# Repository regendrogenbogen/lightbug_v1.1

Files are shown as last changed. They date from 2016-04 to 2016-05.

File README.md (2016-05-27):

# lightbug v1.1

Source files for a small light following robot based on the Arduino Leonardo design. 
Hardware design was done in Altium Designer and I am not sure how and under which license I am
allowed to share the sorce files, therefor I am only sharing the Gerbers, schematic and
the BOM. 
According to the Arduino website derivates of the design must be shared under the
Creative Commons Attribution Share-Alike license, I hope that is applicable for the non-source
files I am publishing. Also, I am not really sure if this really counts as a derivate because I
just took the default operating circuit for the ATMega32U4 and added my peripherals.
The software is of course completely open, according to the GPL license.

Have fun with the files!

The PCB can be ordered at OSH-Park: https://oshpark.com/shared_projects/ZxSDuxPU

I have a blog post to this robot: https://regendrogenbogen.wordpress.com/2016/04/29/lightbug-v1-1/

PS: If I did licence anything wrong and I am violating other licenses, please tell me,
I am still learning!

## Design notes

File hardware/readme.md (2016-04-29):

# Hardware design files for the robot

I added the schematic as an PDF and the gerber files

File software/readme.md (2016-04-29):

# Software for the robot

If you build your own robot, you need to set the fuses correctly. I did this with Atmel Studio.
The Production file for the fuses is "Fuses_Lightbug_v1.1.elf". 
If you can't use Atmel Studio, the fuses need to be the following values:
* Extended: 0xFE
* High: 0xD8
* Low: 0xDE
 
After setting the Fuses and installing the Arduino Leonardo Bootloader (Leonardo-prod-firmware-2012-12-10.hex)
you can program the board like any regular Arduino Leonardo.

There are 2 versions:
* one basic which just has the light following ability (software_lightbug_v1_0)
* one with added serial communication with simple commands to control the robot over bluetooth (software_lightbug_v1_1)

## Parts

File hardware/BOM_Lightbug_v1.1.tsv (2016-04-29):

Positions/quantity | Item | Description | order number
 | Farnell
D1 | STPS3L40S | Schottky diode | 2353680
LED1, LED2 | LED 3mm | green | 1142502
3 | LR6/AA Alkaline | Batteries, 120 pcs. | 2470180
R1, R2 | 1k | Resistor, wired | 9341102
R4, R5 | 330R | Resistor, wired | 9341730
4 | 2k4 | Resistor, SMD, for servo hacking | 9332880
LDR1, LDR2 | LDR | Light sensor | 3168335
R6, R7 | 22R | Resistor, SMD | 9332847
IC1 | ATMEGA32U4 | 8 bit, AVR | 1748525
USB1 | Micro USB socket | Type B | 2293753
C4 | 1uF | Ceramic condensator SMD | 1759422
Y1 | Keramikresonator 16MHz | Ceramic resonator 16 MHz | 2470359
C1, C2 | 100nF | Ceramic condensator SMD | 1759167
C3 | 100nF | Ceramic condensator wired | 2112751
2 | washers 2,7mm | Wheel monting | 2253190
R3, R10 | 10k | Resistor, SMD | 2447553
JP2 | Jumper | Power on jumper | 5217908
S1 | OS102011MS2QN1 | 100mA sliding switch, power selector | 1201430
 | Hobbyking
2 | HK15346 | Servo motors, need to be hacked | HK15346
1 | wheels | Pack of 5 | OR006-00809
 | Pololu
1 | ball caster | 3/8 inch Plastic Ball | 950
 | Distrelec
1 | Battery case | 3 x AA | 973233
1 | pin headers | 5,8mm, 2,6mm | 126387

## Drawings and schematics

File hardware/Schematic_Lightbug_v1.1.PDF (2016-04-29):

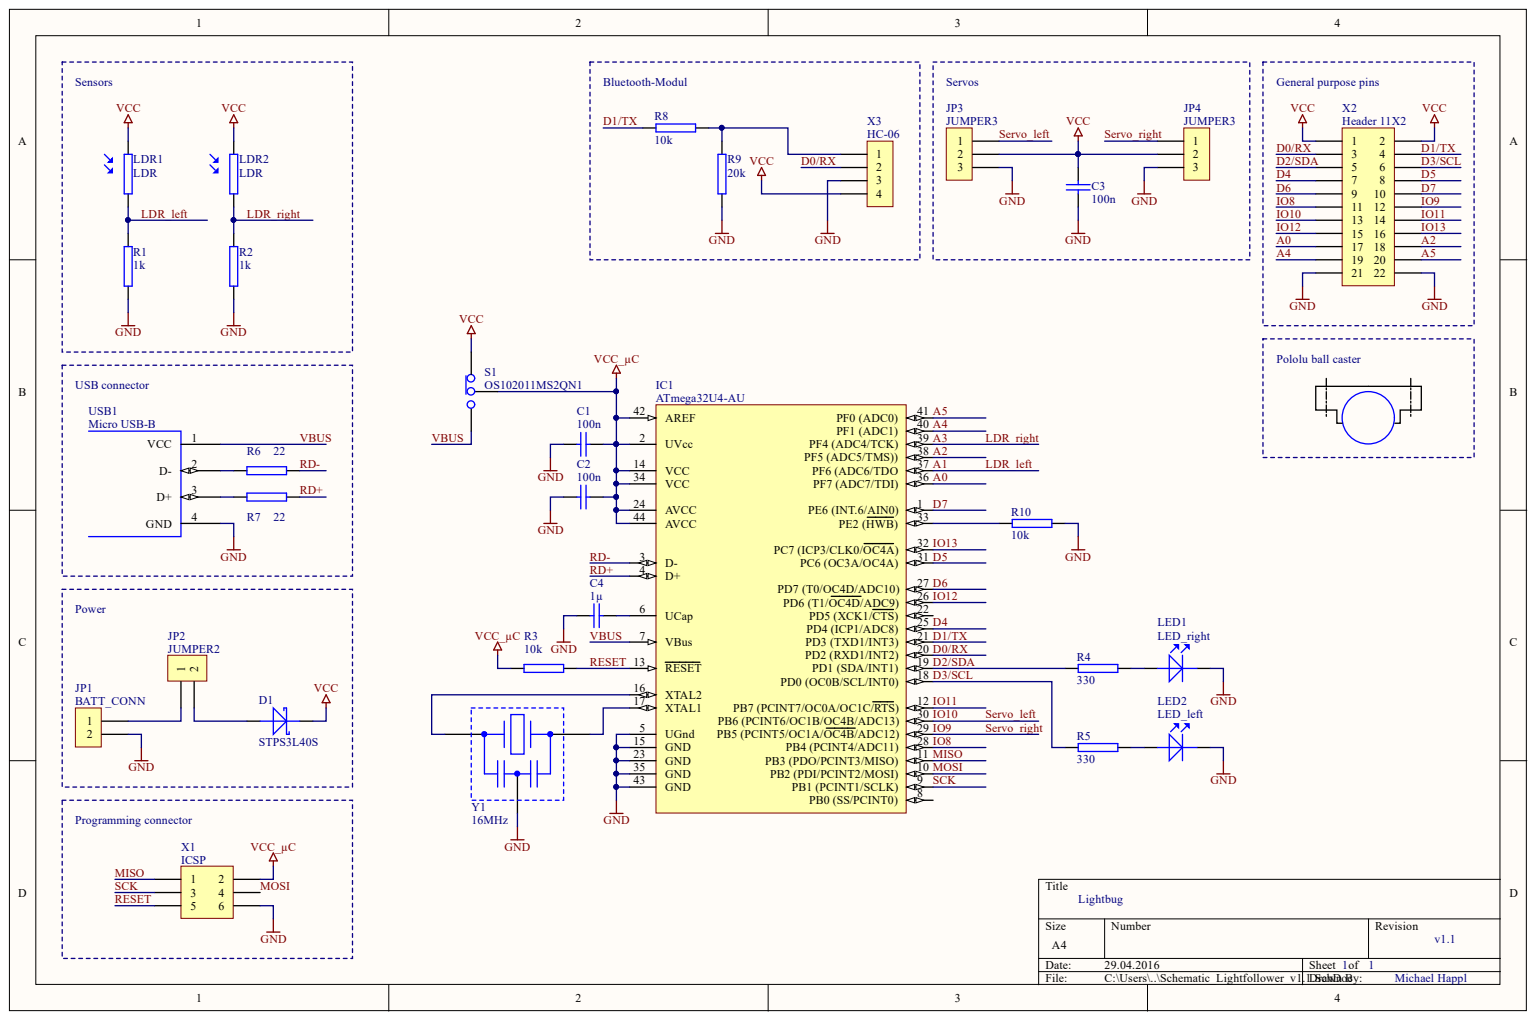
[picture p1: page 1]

XTAL1 17

GND 15 | IO8

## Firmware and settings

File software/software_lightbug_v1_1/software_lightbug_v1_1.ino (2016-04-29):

// Lightbug v 1.1
// by Michael Happl
// based on Lightfollower V1.0 by Johann Leinweber
// Adds a serial communication with simple commands to make it possible
// to control the robot over bluetooth.

#include <Servo.h> 

#define led_left 2           //digital pin for the left LED
#define led_right 3          //digital pin for the right LED
#define led_mode 5           //digital pin for the mode LED
#define servopin_left 10     //digital pin for the left servo
#define servopin_right 9     //didital pin for the right servo
#define servo_high 150       //value for the left servo
#define servo_low 30         //value for the right servo

Servo myservo_left;          //create servo object to control a servo
Servo myservo_right;         //create servo object to control a servo

int left_LDR = A1;           //analog pin used to connect the left LDR
int right_LDR = A3;          //analog pin used to connect the right LDR
int trh_time = 6000;         //time for measuring thresholdvalue in ms
//int time = 0;                //temporary time for measuring time
int val_left = 0;            //variable to read the value from left LDR
int val_right = 0;           //variable to read the value from left LDR
int mean_left = 0;           //meanvalue left LDR
int mean_right = 0;          //meanvalue right LDR
int trh_left = 0;            //threshold for left LDR
int trh_right = 0;           //threshold for right LDR
int loop_time = 10;          //execute loop only every 10ms
unsigned long time = 0;      //variable for measuring time

// State flag
boolean auto_mode = true;

//====================== Serial stuff for the bluetooth module ======================
// constants
#define Baudrate 9600                //baudrate for communicating with the HC-06 Bluetooth module

// variables
boolean debug = 1;                   //Debug mode for testing the commands
boolean command_ok = false;          //indicates finished command receive

char command_string[3];              //the received characters, max. 3
char sensor_left_string[] = "LLX#";  //placeholder for the left sensor value
char sensor_right_string[] = "LRX#"; //placeholder for the rigth sensor value
int char_index = 0;                  //index of the received character


//====================== Setup ======================
void setup()                              //setup, will be executed only once at the start
{   
  pinMode(led_left,OUTPUT);                   //left LED pin as output
  pinMode(led_right,OUTPUT);                  //right LED pin as output
  pinMode(led_mode,OUTPUT);                   //mode LED pin as output
  digitalWrite(led_left, HIGH);               //switch LED left on
  digitalWrite(led_right, HIGH);              //switch LED right on
  digitalWrite(led_mode,LOW);                 //remote controlled mode is off
  delay(5000);                                //wait after power on
  threshold_detect();                         //call routine for thresholddetect
  init_serial();
}                                         //end of setup


//====================== main loop ======================
void loop()                               //main loop
{ 
  receive_characters();                       //receive commands from the bluetooth module
  mode_check();                               //check the command for the current mode
  if ((auto_mode) && (millis() > time))       //run the automatic mode only at a fixed intervall
  {
    time = millis() + loop_time;              //save the current time plus the loop time
    val_left = analogRead(left_LDR);          //left LDR read
    val_right = analogRead(right_LDR);        //right LDR read

    if (val_right > trh_right+40)             //if right LDR is above threshold_right
    {
      servo_left_on(servo_high);              //turn left servo on
    }
    else
    {
      servo_left_off();                       //turn left servo off
    }

    if (val_left > trh_left+40)               //if left LDR is above threshold_left
    {
      servo_right_on(servo_low);              //turn right servo on
    }
    else
    {
      servo_right_off();                      //turn right servo off
    }
    
    sensor_left_string[2] = (char)(val_left / 4);
    send_serial(sensor_left_string);          //send the current left sensor value to the app
    sensor_right_string[2] = (char)(val_right / 4);
    send_serial(sensor_right_string);         //send the current right sensor value to the app
  }                                           //end of automatic mode
  else                                        //begin of remote controlled mode
  { 
    if (command_ok)                           //only if the current command is correct
    {
      if (command_string == "MLF")            //forward left motor
        servo_left_on(servo_high);
      if (command_string == "MLR")            //reverse left motor
        servo_left_on(servo_low);
      if (command_string == "MLO")            //stop left motor
        servo_left_off();
      if (command_string == "MRF")            //forward right motor
        servo_right_on(servo_high);
      if (command_string == "MRR")            //reverse right motor
        servo_right_on(servo_low);
      if (command_string == "MRO")            //stop right motor
        servo_right_off();
    }
  }
}                                         //end of main loop

//====================== servo routines ======================

void servo_left_on (int servo_value)      //routine for turning the left servo on
{
      myservo_left.attach(servopin_left);     //attaches the left servo on pin "left" to the servo object
      myservo_left.write(servo_value);        //left servo turn left
      digitalWrite(led_left, HIGH);           //left LED on
      if (servo_value < 90)
      {
        send_serial("MLR#");                  //send motor left direction to app
      }
      else
      {
        send_serial("MLF#");                  //send motor left direction to app
      }
}                                         //end of servo left on


void servo_left_off ()                    //routine for turning the left servo off
{
      myservo_left.detach();                  //deactivate left servo
      digitalWrite(led_left, LOW);            //left LED off
      send_serial("MLO#");                    //send motor left off to app
}                                         //end of servo left off


void servo_right_on (int servo_value)     //routine for turning the right servo on
{
      myservo_right.attach(servopin_right);   //attaches the right servo on pin "right" to the servo object
      myservo_right.write(servo_value);       //right servo turn right
      digitalWrite(led_right, HIGH);          //right LED on
      if (servo_value < 90)
      {
        send_serial("MRF#");                  //send motor right direction to app
      }
      else
      {
        send_serial("MRR#");                  //send motor right direction to app
      }
}                                         //end of servo right on


void servo_right_off ()                   //routine for turning the right servo off
{
      myservo_right.detach();                 //deactivate right Servo
      digitalWrite(led_right, LOW);           //right LED off
      send_serial("MRO#");                    //send motor right off to app
}                                         //end of servo right off


void threshold_detect ()                  //routine for looking for the average brightness
{
  servo_left_on(servo_high);                 //left servo turn left

  time = millis();
  do
  {
    mean_left = 0;                            //reset variables
    mean_right = 0;                           //reset variables
    for (int i = 0; i<5; i++)                 //5 runs do get average offsetvalues from LDRs
    {
      mean_left += analogRead(left_LDR);      //sum
      mean_right += analogRead(right_LDR);    //sum
    }
    mean_left /= 5;
    mean_right /= 5;

    trh_left = max(trh_left,mean_left );      //get max value while rotating
    trh_right = max(trh_right,mean_right );   //get max value while rotating
  } 
  while (millis() < time + trh_time);         //do for the desired time, until one round is done

  servo_left_off();                           //turn left servo off
}                                         //end of the routine

//====================== communication stuff ======================

void init_serial ()                       //setup the serial connection
{
  if (debug)                                  //when debugging, use the serial over USB
  {
    Serial.begin(Baudrate);
  }
  else                                        //otherwise use the hardware UART
  {
    Serial1.begin(Baudrate);
  }
}                                         //end of serial setup


void send_serial (char send_string[4])    //routine for sending replies
{
  if (debug)                                  //when debugging, use the serial over USB
  {
    Serial.print(send_string);
  }
  else                                        //otherwise use the hardware UART
  {
    Serial1.print(send_string);
  }
}                                         //end of send routine


void receive_characters ()                //handler for the received characters    
{
  if(Serial1.available())                     //Data available at UART?
  {
    char ch = Serial1.read();                 //save the received character
    if ((ch == '#') && (char_index == 3))     //delimiter and last character?
    { 
      command_ok = true;                      //then the command must be correct
      char_index = 0;                         //reset the index counter
    }
    else                                      //for all other characters:
    {
      command_ok = false;                     //reset the flag
      if (char_index <= 2)                    //index in the correct range?
      {
        command_string[char_index] = ch;      //append to the command string
        char_index++;                         //increase the index
        
      }                                       //if out of range
      else char_index = 0;                    //reset the index counter
    }
  }                                   
}                                         //end of receive handler


void mode_check ()                        //mode switcher for the automatic/remote mode
{
  if (command_ok)                             //only when the command is ok
  {
    if (command_string == "AON")              //check for the right commands
    {                                         //automatic mode on?
      auto_mode = true;
      digitalWrite(led_mode,LOW);             //mode LED is OFF for automatic mode
      command_ok = false;                     //reset the flag so the command is executed only once
    }
    if (command_string == "AON")              //automatic mode off?
    {                                         
      auto_mode = false;
      digitalWrite(led_mode,LOW);             //mode LED is ON for remote controlled mode
      command_ok = false;                     //reset the flag so the command is executed only once
    }
  }
}                                         //end of mode switcher
